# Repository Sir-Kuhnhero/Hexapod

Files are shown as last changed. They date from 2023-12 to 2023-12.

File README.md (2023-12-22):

Due to bandwidth limitations I was forced to remove some files. If you can't download some of the larger files, go to Printables. You should find the most important files there.
Printables: https://www.printables.com/model/606030-3d-printed-hexapod

# Overview #

Seems like you want to build a Hexapod. Don't know why but since you're here, might as well tell you about the most important features about my design:

1. Cheap: 120 € (see Parts (toBuy) file)
2. RGB: 271 individual RGB LEDs
3. Cable management: Cables are routed inside the leg. no cable loop that tangle
4. ORP compatible: compatible with the Open Robotic Platform modules
5. Bluetooth control: Remote control via phone app

If this hasn't convinced you might I suggest watching my videos on the design and build.

Leg: https://youtu.be/Ta3ILBvA57U

Body & first Steps: https://youtu.be/FBk1Pa01zQ4

# Build #

Since you are reading this I assume you are at least considering my design. I have some instructions on Instucatbles and Hackster.io if you want to take a look at that.
Instructables: https://www.instructables.com/3D-Printed-Hexapod/
Hackster.io: https://www.hackster.io/sir-kuhnhero/3d-printed-hexapod-05a60c

You can also find all the most important files on Printables: https://www.printables.com/model/606030-3d-printed-hexapod

All the 3mf files are oriented correctly with the needed support material. My parts are design in a way that uses minimal support material. See “Parts (toPrint)” Excel sheet.

If you don't know what and where to buy take a look at the "Parts (toBuy)" Excel sheet. Those are the parts I bought and where. You can also update the prices and it will automatically calculate the final price. Everything I listed is without shipping since that varies drastically.

If I didn't buy it or the link doesn't work anymore I linked to where I would buy.

# Wiring #



Connect everything like in the wiring diagram above. Be sure to use shielded wire for the connection between the STM32 and the servo drivers. I had some problems with interference without it.

One thing missing here is the XT60 connection between the battery and the rest of the circuit. You need a way to shut the hexapod down.

The LEDs are all connected in series in this order: Eye Centre, Eye middle ring, Eye outer ring, bottom ring, leg[ (front right) root -> tip (proceeding clockwise)

For the servos you can connect them to wherever is easiest. However you will need to set the channel for each servo in the "output.cpp" file correctly.

```
Leg[0].Servo[0].ch = 2;
Leg[0].Servo[1].ch = 1;
Leg[0].Servo[2].ch = 0;

Leg[1].Servo[0].ch = 6;
Leg[1].Servo[1].ch = 5;
Leg[1].Servo[2].ch = 4;

Leg[2].Servo[0].ch = 13;
Leg[2].Servo[1].ch = 14;
Leg[2].Servo[2].ch = 15;

Leg[3].Servo[0].ch = 18;
Leg[3].Servo[1].ch = 17;
Leg[3].Servo[2].ch = 16;

Leg[4].Servo[0].ch = 25;
Leg[4].Servo[1].ch = 26;
Leg[4].Servo[2].ch = 27;

Leg[5].Servo[0].ch = 29;
Leg[5].Servo[1].ch = 30;
Leg[5].Servo[2].ch = 31;
```

The Leg naming is as followes:

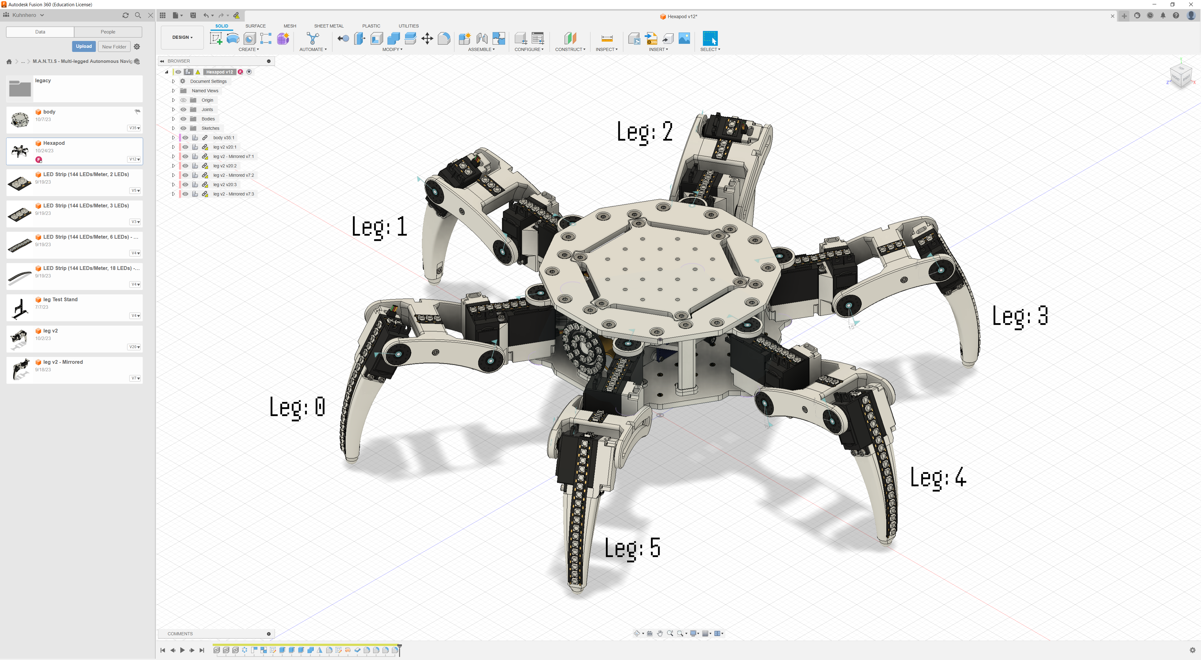
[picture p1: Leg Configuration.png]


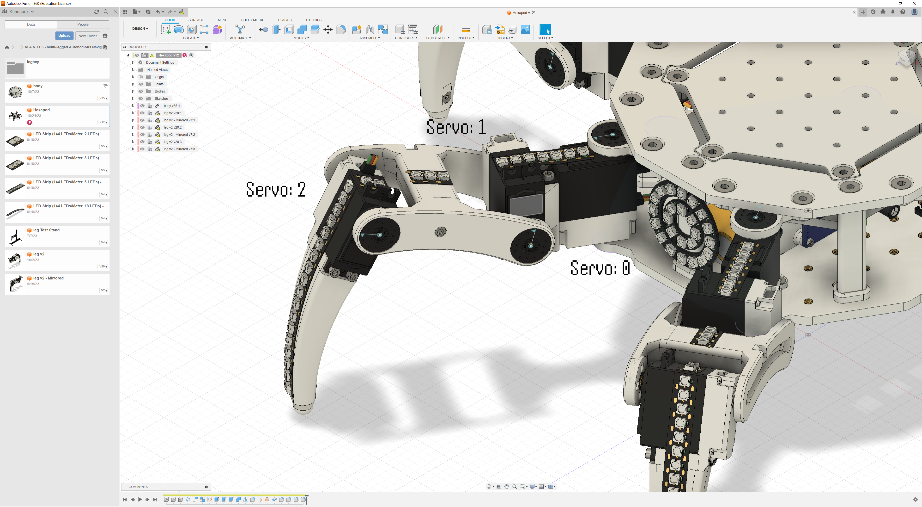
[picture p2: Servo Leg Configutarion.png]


On that node ensure that you bridge the first solder pad on one of the servo drivers. This will ensure that it uses a different I2C address. This second driver will continue the channel numbering of the first (16-31).

# Programming #

The code has been written in Visual Studio Code with the platform IO extension.

To Upload it make sure you have both installed and add the folder bellow as a project.

From here upload the code. Be sure to use an ST-Link for this. You can use a simple FTDI Programmer or something similar but you will have to unplug the Bluetooth module to connect it and change the "upload_protocol" in the platformio.ini file from "stlink" to what your programmer requires. Check [here](https://docs.platformio.org/en/latest/boards/ststm32/genericSTM32F103C8.html#board-ststm32-genericstm32f103c8) for more info.

```
[env:genericSTM32F103C8]
platform = ststm32
board = genericSTM32F103C8
framework = arduino
debug_tool = stlink
upload_protocol = stlink
lib_deps = 
  adafruit/Adafruit PWM Servo Driver Library@^2.4.1
  fastled/FastLED@^3.6.0
 ```

I had some issues with my ST-Link a while ago and had to switch to an FTDI programmer. This ended up looking like this:

```
[env:genericSTM32F103C8]
platform = ststm32
board = genericSTM32F103C8
framework = arduino
upload_protocol = serial
lib_deps = 
  adafruit/Adafruit PWM Servo Driver Library@^2.4.1
  fastled/FastLED@^3.6.0
 ```

If you want to deactivate some functions, for example the LEDs, for some reason you can do that in the "header.h" file by commenting out what you don’t want. This can be great for testing new features.

```
#define WS2812B_LED

#define SERVO
//#define SERVO_CALIBRATION

#define DEBUG
// #define DEBUG_SERIAL
// #define DEBUG_LED

#define BLUETOOTH
```

You will also need to fine tune the servo angles by setting the angleOffset for each servo in the output.cpp file. If you set your values correctly it should look something like this. To make this easier you can uncomment "#define SERVO_CALIBRATION" in the "header.h" file. This will move every leg to it's origin.

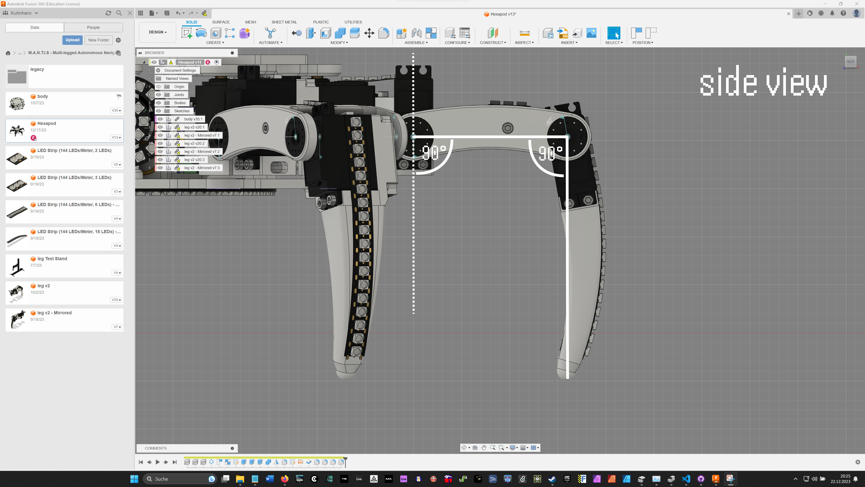
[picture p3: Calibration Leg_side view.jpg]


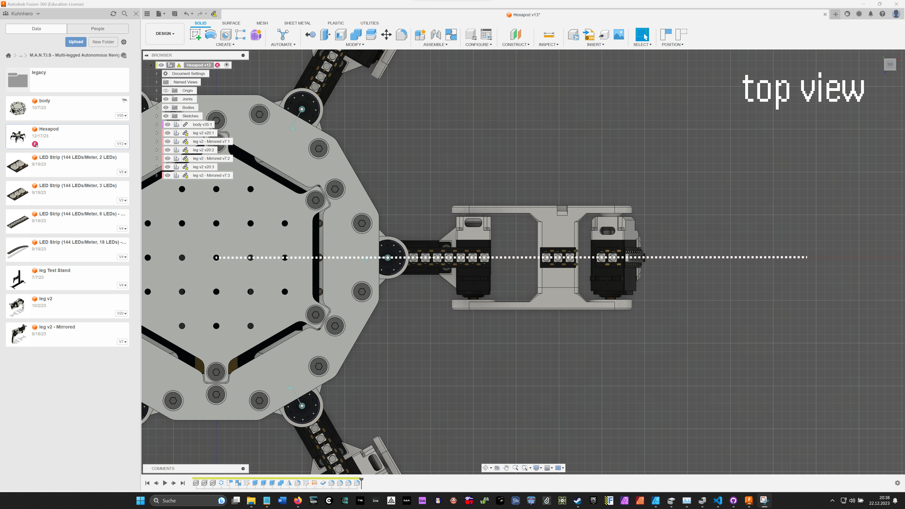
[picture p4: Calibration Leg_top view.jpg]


# Install Remote App & Connecting #

If you install the application you will get a message saying this might be dangerous to install. This is normal so don't worry. If you don't trust me take a look at the MIT App Inventor project files and compile it yourself.

Once installed make sure to allow "Nearby Devices". This is required for the app to find available Bluetooth devices.

Note that there are slider for controlling the Hexapods LEDs but that is currently disabled to reduce latency.

Turn your Hexapod on and pair to the Bluetooth module in you phones Bluetooth settings (only do this once). The default password is 1234 or 0000.

Now open the Hexapod Remote app and connect to the Bluetooth module. Once connected the Hexapod will have a simple startup animation and now you can control the hexapod using the two sticks.

Note that if you have changed something with #define at the beginning of header.h this behaviour might be different.

# Issues #

To be clear, my design is NOT perfect. Here are all the problems I have:

1. highly integrated leg design: routing the cables inside the leg looks awesome but makes assembly more difficult. If you were to not use LEDs this problem would largely be negated.
2. Current spikes: the hexapod is able to handle some load but especially at times of a power spike the Buck converter powering the servos can be insufficient. So you might want to use two or buy a more powerful one.
3. I2C buss instability: I had problems with the I2C buss between the STM32 and servo drivers breaking down causing the Hexapod to freeze. I was able to fix that by using shielded cables, but it required some trial and error.
4. incomplete Code: Not all features have been added in code. For example no LED animations beside the startup animation.

If you have any questions or suggestions consider writing me a comment.

Happy Making :)

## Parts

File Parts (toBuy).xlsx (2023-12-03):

 | Type | Lenght (mm) | number | price x1 (€) | price total (€) | Link (all provided links are where I bought or would buy and likely not the cheapest option). Prices may vary based on where, when and how you buy. If these Links are no longer valid just search for the Type.
Screws | M2 (Cub head) | 6 | 8 | 0.0248 | 0.1984 | https://www.aliexpress.com/item/1005001975621423.html
 | M3 (Cub head) | 10 | 12 | 0.0418 | 0.1672 | https://www.aliexpress.com/item/1005001975621423.html
 | M3 (Cub head) | 14 | 12 | 0.052 | 0.624 | https://www.aliexpress.com/item/1005001975621423.html
 | M3 (Cub head) | 20 | 6 | 0.0628 | 0.7536 | https://www.aliexpress.com/item/1005001975621423.html
 | M3 (Cub head) | 30 | 12 | 0.0792 | 0.4752 | https://www.aliexpress.com/item/1005001975621423.html
 | M3 (Countersunk) | 6 | 4 | 0.026 | 0.312 | https://www.aliexpress.com/item/4000020967604.html
 | M3 (Countersunk) | 10 | 4 | 0.0324 | 0.1296 | https://www.aliexpress.com/item/4000020967604.html
 | M5 (Countersunk) | 10 | 30 | 0.0382 | 1.146 | https://www.aliexpress.com/item/4000020967604.html
 | M3 nut (Square) |  | 48 | 0.0212 | 1.0176 | https://www.aliexpress.com/item/1005002179121598.html
 | M3 heat set insert (OD 5) | 5 | 53 | 0.0252 | 1.3356 | https://www.aliexpress.com/item/1005004490656289.html |  | You will only need 8 to build the Hexapod. The rest are for adding potential modules in the future
 | M5 heat set insert (OD 7) | 5 | 42 | 0.0502 | 2.1084 | https://www.aliexpress.com/item/1005004490656289.html
Electronics | STM32...C8T6 (BluePill) |  | 1 | 1.58 | 1.58 | https://www.aliexpress.com/item/1005003169244854.html
 | HC-05 |  | 1 | 2.11 | 2.11 | https://de.aliexpress.com/item/32967247206
 | PCA9865 (Servo driver) |  | 2 | 2.51 | 5.02 | https://www.aliexpress.com/item/32466332558.html
 | XL4016E1 (Buck converter) |  | 1 | 4.5 | 4.5 | https://www.aliexpress.com/item/33051908449.html
 | XL6009 (Blue Good) |  | 1 | 1.51 | 1.51 | https://de.aliexpress.com/item/1005005967596775.html
 | LED Ring | 60 | 1 | 5.83 | 5.83 | https://www.aliexpress.com/item/1005003185980117.html
 | LED Ring | 16 | 1 | 3 | 3 | https://www.aliexpress.com/item/4000877848238.html
 | LED Ring | 8 | 1 | 2 | 2 | https://www.aliexpress.com/item/4000877848238.html
 | LED Strip | 144LEDs/m | 2 | 7.28 | 14.56 | https://www.aliexpress.com/item/1005004129769604.html
 | 18650 Battery |  | 4 | 3.99 | 15.96 | https://www.18650batterystore.com/products/samsung-25r-18650
 | HX-2S-JH20 |  | 1 | 0.81 | 0.81 | https://www.aliexpress.com/item/1005002320527374.html
 | Wire | 1 m | 1 | 2.28 | 2.28 | https://www.aliexpress.com/item/1005001568846789.html
 | Wire | 1 m | 1 | 1.13 | 1.13 | https://www.aliexpress.com/item/1005001568846789.html
 | MGN996 Servo |  | 18 | 2.85 | 51.3 | https://www.aliexpress.com/item/33055771986.html
 | XT60 Female |  | 1 | 0.78 | 0.78 | https://www.aliexpress.com/item/1005003284718240.html
 | XT60 Male |  | 1 | 0.78 | 0.78 | https://www.aliexpress.com/item/1005003284718240.html
 |  |  |  |  | Total: |  | Shiping estimate:
 |  |  |  |  | 121.4176 |  | 0
 |  |  |  |  | Total (including Shiping estimate):
 |  |  |  |  | 121.4176
 | You will also need an ST-Link (or some other programmer) and a Phone.
Everything bellow are the parts above, only sorted for each subcomponent like Leg & Body and might be incomplete
Single Leg
Screws | Type | Length (mm) | number
 | M3 (Cub head) | 10 | 2
 | M3 (Cub head) | 14 | 2
 | M3 (Cub head) | 20 | 1
 | M3 (Cub head) | 30 | 2
 | M3 (Countersunk) | 10 | 1
 | M3 nut (Square) |  | 8
 | M5 heat set insert | 5 | 2
Electronics | LED Strip (LEDs) |  | 31
 | MGN996 Servo |  | 3
Body
Screws | Type | Lenght (mm) | number
 | M2 (Cub head) | 6 | 8
 | M3 (Countersunk) | 6 | 4
 | M3 (Countersunk) | 10 | 4
 | M5 (Countersunk) | 10 | 30
 | M3 heat set insert | 5.5 | 74
 | M5 heat set insert | 5 | 30
Electronics | STM32 (BluePill)
 | PCA9865 (Servo driver) |  | 2
 | XL4016E1 (Buck converter) |  | 1
 | LED ring 60 |  | 1
 | LED ring 16 |  | 1
 | LED ring 8 |  | 1
 | LED Strip (LEDs) |  | 1
 | 18650 Battery |  | 4
 | HX-2S-JH20 |  | 1
 | Wire
 | Wire

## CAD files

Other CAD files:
Hexapod_3D Models/body main_bottom.3mf
Hexapod_3D Models/body main_top.3mf
Hexapod_3D Models/leg/PLA_Tibia_main.3mf
Hexapod_3D Models/body/PLA_body spacer.3mf
Hexapod_3D Models/bushing_set.3mf
Hexapod_3D Models/leg Test Stand/test stand_mount.3mf
Hexapod_3D Models/leg/PLA_bushing.3mf
Hexapod_3D Models/body/body v35.3mf
Hexapod_3D Models/leg Test Stand/PLA-Coxa_bottom.3mf
Hexapod_3D Models/leg/PLA_Femur_left_mirrored.3mf
Hexapod_3D Models/leg_set_mirrored.3mf
Hexapod_3D Models/Hexapod v8.3mf
Hexapod_3D Models/leg Test Stand/PLA-90° Cuppler (40mm).3mf
Hexapod_3D Models/leg/PLA-Trochanter_Servo mount_mirrored.3mf
Hexapod_3D Models/leg Test Stand/leg Test Stand v4.3mf
Hexapod_3D Models/leg/PLA_Femur_right_mirrored.3mf
Hexapod_3D Models/leg Test Stand/test stand foot.3mf
Hexapod_3D Models/leg/PLA-Coxa_top.3mf
Hexapod_3D Models/Hexapod v8-rotated.3mf
Hexapod_3D Models/Hexapod v8.f3z
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

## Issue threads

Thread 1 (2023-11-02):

FastLED

Mordenkainen, 2023-11-02:
Was there something special to do to get the FastLED library working?

I am trying just a simple blink app and while it compiles and loads, no pin seems to be outputting the data signal. Was there a special version or something you used?

Mordenkainen, 2023-11-02:
User Error! SRY.

Closed 2023-11-02.

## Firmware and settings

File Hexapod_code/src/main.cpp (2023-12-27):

#include <Arduino.h>
#include <header.h>

int loopTime;

Vector2 directionInput(0, 0);
float rotationInput = 20;
float groundClearance = 35;
float stepRadius = 100;
float maxSpeed = 90;

State HexapodState = State::SITTING;

#ifdef WS2812B_LED
int ledUpdateTimer = 0;
int brightness = 5;
int colorR = 0;
int colorG = 0;
int colorB = 255;
bool ledUpdate = true;
#endif

void setup()
{
#ifdef BLUETOOTH
  Bluetooth_init();

  // don't continue until a connection has been established and a array of data has been recived
  while (Data[DATA_LENGTH - 1] == 0) // no data send can be 0
  {
    Bluetooth_read();
    delay(1);
  }

  Bluetooth_map();
#endif

#ifdef WS2812B_LED // initialitze LEDs
  Led_init();
#endif

#ifdef SERVO // initialite Servos
  Servo_init();
#endif

#ifdef WS2812B_LED // startup LED animation
  for (size_t i = 0; i < 25; i++)
  {
    Led_update(i);
    FastLED.show();
    delay(25);
  }

#ifdef SERVO
  for (int i = 0; i < 100; i++)
  {
    for (int o = 0; o < 6; o++)
    {
      LED_leg_animation(o, 0, float(i + 1) / 100.0f);
    }
    FastLED.show();

    delay(10);
  }
#endif

#endif

#ifdef SERVO
#ifdef BLUETOOTH
  Bluetooth_clear();
  Data[0] = 50;

  while (Data[0] == 50) // is 50 when it should sit down and 100 when it should stand up
  {
    Bluetooth_read();
    delay(10);
  }

  standUp();
#endif
#endif

#ifdef SERVO_CALIBRATION
  HexapodState = State::STANDING;
#endif
}

void loop()
{
  int long curTime = millis();

#ifdef BLUETOOTH
  Bluetooth_read();
  Bluetooth_map();
#endif

#ifdef SERVO

  // stand up and sit down as input suggests
  if (Data[0] == 50 && (HexapodState == State::STANDING || HexapodState == State::WALKING))
  {
    sitDown();
    curTime = millis(); // the sitDown function takes time so loopTime gets messed up
  }
  else if (Data[0] == 100 && HexapodState == State::SITTING)
  {
    standUp();
    curTime = millis(); // the sitDown function takes time so loopTime gets messed up
  }

  if (HexapodState == State::STANDING || HexapodState == State::WALKING)
  {
    walkCycle();
    Output_update();
  }
#endif

#ifdef WS2812B_LED
  // ping pong led blue color
  /*
    if (colorBDirection == 0)
    {
      colorB--;
    }
    else if (colorBDirection == 1)
    {
      colorB++;
    }

    if (colorB == 0)
    {
      colorBDirection = 1;
    }
    else if (colorB == 255)
    {
      colorBDirection = 0;
    }
  */

  if (ledUpdate || (ledUpdateTimer > updateInterval && continuesUpdate))
  {

    for (size_t i = 0; i < NUM_LEDS; i++)
    {
      Led_update(i);
    }

    FastLED.setBrightness(brightness);
    FastLED.show();

    ledUpdate = false;
    ledUpdateTimer = 0;

#ifdef BLUETOOTH
    // Bluetooth_clear(); // updating every led takes time
#endif
    curTime = millis();
  }

  ledUpdateTimer += loopTime;
#endif

  loopTime = millis() - curTime;
}

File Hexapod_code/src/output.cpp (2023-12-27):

#include <Arduino.h>
#include "header.h"

// ================================================================
// ===                          Servo                           ===
// ================================================================
#ifdef SERVO

Adafruit_PWMServoDriver servoDriver_0 = Adafruit_PWMServoDriver();
Adafruit_PWMServoDriver servoDriver_1 = Adafruit_PWMServoDriver(0x41);

Leg_Struct Leg[6];

void Servo_init()
{
    servoDriver_0.begin();
    servoDriver_0.setOscillatorFrequency(27000000);
    servoDriver_0.setPWMFreq(SERVO_FREQ); // Analog servos run at ~50 Hz updates

    servoDriver_1.begin();
    servoDriver_1.setOscillatorFrequency(27000000);
    servoDriver_1.setPWMFreq(SERVO_FREQ); // Analog servos run at ~50 Hz updates

#pragma region configureServos

// for correct Servo Placenment check the Leg Configuration and Servo Leg Configuration Images
#pragma region Leg_0
    Leg[0].Servo[0].ch = 2;
    Leg[0].Servo[1].ch = 1;
    Leg[0].Servo[2].ch = 0;

    Leg[0].Servo[2].minAngle = 20;
    Leg[0].Servo[2].maxAngle = 160;

    Leg[0].Servo[0].angleOffset = 0;
    Leg[0].Servo[1].angleOffset = -10;
    Leg[0].Servo[2].angleOffset = -5;

    Leg[0].mirrored = true;
    Leg[0].mountAngle = -30;

    Leg[0].minLED = 85;
    Leg[0].maxLED = 115;
#pragma endregion

#pragma region Leg_1
    Leg[1].Servo[0].ch = 6;
    Leg[1].Servo[1].ch = 5;
    Leg[1].Servo[2].ch = 4;

    Leg[1].Servo[2].minAngle = 20;
    Leg[1].Servo[2].maxAngle = 160;

    Leg[1].Servo[0].angleOffset = -10;
    Leg[1].Servo[1].angleOffset = 0;
    Leg[1].Servo[2].angleOffset = 12;

    Leg[1].mirrored = true;
    Leg[1].mountAngle = -90;

    Leg[1].minLED = 116;
    Leg[1].maxLED = 146;
#pragma endregion

#pragma region Leg_2
    Leg[2].Servo[0].ch = 13;
    Leg[2].Servo[1].ch = 14;
    Leg[2].Servo[2].ch = 15;

    Leg[2].Servo[2].minAngle = 20;
    Leg[2].Servo[2].maxAngle = 160;

    Leg[2].Servo[0].angleOffset = -12;
    Leg[2].Servo[1].angleOffset = -10;
    Leg[2].Servo[2].angleOffset = -16;

    Leg[2].mirrored = true;
    Leg[2].mountAngle = -150;

    Leg[2].minLED = 147;
    Leg[2].maxLED = 177;
#pragma endregion

#pragma region Leg_3
    Leg[3].Servo[0].ch = 18;
    Leg[3].Servo[1].ch = 17;
    Leg[3].Servo[2].ch = 16;

    Leg[3].Servo[2].minAngle = 20;
    Leg[3].Servo[2].maxAngle = 160;

    Leg[3].Servo[0].angleOffset = -1;
    Leg[3].Servo[1].angleOffset = 6;
    Leg[3].Servo[2].angleOffset = 44;

    Leg[3].mirrored = false;
    Leg[3].mountAngle = 150;

    Leg[3].minLED = 178;
    Leg[3].maxLED = 208;
#pragma endregion

#pragma region Leg_4
    Leg[4].Servo[0].ch = 25;
    Leg[4].Servo[1].ch = 26;
    Leg[4].Servo[2].ch = 27;

    Leg[4].Servo[2].minAngle = 20;
    Leg[4].Servo[2].maxAngle = 160;

    Leg[4].mirrored = false;
    Leg[4].mountAngle = 90;

    Leg[4].Servo[0].angleOffset = -5;
    Leg[4].Servo[1].angleOffset = -10;
    Leg[4].Servo[2].angleOffset = -8;

    Leg[4].minLED = 209;
    Leg[4].maxLED = 239;
#pragma endregion

#pragma region Leg_5
    Leg[5].Servo[0].ch = 29;
    Leg[5].Servo[1].ch = 30;
    Leg[5].Servo[2].ch = 31;

    Leg[5].Servo[2].minAngle = 20;
    Leg[5].Servo[2].maxAngle = 160;

    Leg[5].Servo[0].angleOffset = -2;
    Leg[5].Servo[1].angleOffset = 3;
    Leg[5].Servo[2].angleOffset = -20;

    Leg[5].mirrored = false;
    Leg[5].mountAngle = 30;

    Leg[5].minLED = 240;
    Leg[5].maxLED = 270;

#pragma endregion
    for (int i = 0; i < int(sizeof(Leg) / sizeof(Leg[0])); i++)
    {
        Leg[i].Servo[1].minAngle = 0;
        Leg[i].Servo[1].maxAngle = 180;
    }

#pragma endregion
}

void Servo_update(const Servo_Struct &servo, const int &onValue)
{
    int angle = constrain(servo.targetAngle, servo.minAngle, servo.maxAngle);
    // check which servo driver to use
    if (servo.ch < 16)
        servoDriver_0.setPWM(servo.ch, onValue, SERVO_BASELINE + (angle + servo.angleOffset) * 2);
    else if (servo.ch < 32)
        servoDriver_1.setPWM(servo.ch - 16, onValue, SERVO_BASELINE + (angle + servo.angleOffset) * 2);
}

void Servo_update(const int &servoCH, const int &angle, const int &onValue)
{
    // check which servo driver to use
    if (servoCH < 16)
        servoDriver_0.setPWM(servoCH, onValue, SERVO_BASELINE + angle * 2);
    else if (servoCH < 32)
        servoDriver_1.setPWM(servoCH - 16, onValue, SERVO_BASELINE + angle * 2);
}

// turns off the output for the servo
void Servo_deactivateAll()
{
    // loop through each leg
    for (size_t i = 0; i < 6; i++)
    {
        // loop through each servo in leg
        for (size_t o = 0; o < 3; o++)
        {
            Servo_update(Leg[i].Servo[o], 4096);
        }
    }
}

// used to test wether min values are correct
void Servo_moveAllToMinValue()
{
    // loop through each leg
    for (size_t i = 0; i < 6; i++)
    {
        // loop through each servo in leg
        for (size_t o = 0; o < 3; o++)
        {
            int oldTargetAngle = Leg[i].Servo[o].targetAngle;

            Leg[i].Servo[o].targetAngle = Leg[0].Servo[o].minAngle - abs(Leg[0].Servo[o].angleOffset);

            Servo_update(Leg[i].Servo[o]);

            Leg[i].Servo[o].targetAngle = oldTargetAngle;
        }
    }
}

// used to test wether max values are correct
void Servo_moveAllToMaxValue()
{
    // loop through each leg
    for (size_t i = 0; i < 6; i++)
    {
        // loop through each servo in leg
        for (size_t o = 0; o < 3; o++)
        {
            int oldTargetAngle = Leg[i].Servo[o].targetAngle;

            Leg[i].Servo[o].targetAngle = Leg[0].Servo[o].maxAngle + abs(Leg[0].Servo[o].angleOffset);

            Servo_update(Leg[i].Servo[o]);

            Leg[i].Servo[o].targetAngle = oldTargetAngle;
        }
    }
}

void Leg_update(const int &legID)
{
    calcLegServoAngles(Leg[legID]);

    Servo_update(Leg[legID].Servo[0]);
    Servo_update(Leg[legID].Servo[1]);
    Servo_update(Leg[legID].Servo[2]);
}

// update every output as needed to reflect any changes
void Output_update()
{
    Leg_update(0);
    Leg_update(1);
    Leg_update(2);
    Leg_update(3);
    Leg_update(4);
    Leg_update(5);
}

#endif

// ================================================================
// ===                           LED                            ===
// ================================================================
#ifdef WS2812B_LED

CRGB leds[NUM_LEDS];

void Led_init()
{
    FastLED.addLeds<WS2812B, DATA_PIN, RGB>(leds, NUM_LEDS); // GRB ordering is typical

    FastLED.setBrightness(brightness);

    // turn all led off
    for (size_t i = 0; i < NUM_LEDS; i++)
    {
        leds[i] = CRGB::Black;
    }
    FastLED.show();
}

void Led_update(const int &ledID)
{
    leds[ledID] = CRGB(uint8_t(float(colorG) * 2.5f), uint8_t(float(colorR) * 2.5f), uint8_t(float(colorB) * 2.5f));
}

void Led_update(const int &ledID, CRGB color)
{
    leds[ledID] = color;
}
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

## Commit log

2023-01-24 servo actuator
2023-08-24 3d models
    [Coxa-bottom.3mf, Coxa-top.3mf, Femur-Servo mount.3mf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]
2023-08-26 full Hexapod framework
    IK for the each leg of the full hexapod has been finished. No full Hexapod IK has been implemented. LEDs and startup sequence have been implemented.
2023-08-29 fixed IK, added circleProjection
    Fixed an issue that made it impossible to move the legs in the y axis. There is now also a function to project a point onto a sphere through a vector (not fully tested).
    [debug.cpp, header.h, ik.cpp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]
2023-09-01 added basic walking
    the hexaod can now take steps. Lifting the legs is still very unsmothe and sudden but changes are in the works
2023-09-03 walking now working
    The Hexapod now properly lift it's legs for each steps. This works in every direction.
2023-09-09 code cleanup
    removed some unused code and added a way to use an external arduino as a crude debugger
2023-09-11 walk gait restructure
    very simmilar code as before only more readable. Additionally the leg calculation is done for each leg in preperation for rotation
2023-09-12 improved walking start
    Hexapod now starts liften each leg to maximise the length of the first step
2023-09-12 partial rotation
    Legs are moving in a concentric circle. However for some reason the Path of Leg 0 & 5 as well as 2 & 3 are swaped.
    [header.h, main.cpp]
2023-09-12 rotation working
    Turns out there was a missplaced - in the inverse kinematics :)
2023-09-14 correct movement
    Values received are now correctly converted to value input for the walking algorithm
    [header.h, main.cpp]
2023-09-17 more remote features
    Some more features for controlling the Hexapod. The LEDs are not working for some reason. They are just alway white with 100% brightness.
    [header.h, main.cpp, output.cpp]
2023-09-28 LED controll
    User can now in theory controll the color and brightness of the LEDs. However this has been deactivated to lower latency and make the hexapod movements more responsive.
2023-10-07 addded 3d models
    updated 3d models are now included
    [Hexapod v8-rotated.3mf, Hexapod v8.3mf, Hexapod v8.f3z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]
2023-10-08 Aditional files
    More models and MIT App Inventor source code.
    [PLA-Trochanter_Servo mount_mirrored.3mf, PLA-Trochanter_Servo mount_mirrored.stl, PLA_Femur_left_mirrored.3mf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]
2023-10-08 wiring diagram
2023-11-02 removed some large files
    I removed some large files since GitHub only allows for a specific ammount of bandwith.
    [Coxa-bottom.3mf, Coxa-top.3mf, Femur-Servo mount.3mf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]
2023-11-08 missing Bluetooth module
    [Parts (toBuy).xlsx]
2023-12-03 Parts (toBuy) list
    [Parts (toBuy).xlsx]
2023-12-17 Leg and Servo Configuration
2023-12-22 Add Calibration routine
    I previously remove my code for calibration the servo offset. You can now simply uncomment #define SERVO_CALIBRATION to tell go into servo calibration mode
    [Mustache.3mf, PLA-90° Cuppler (40mm).stl, PLA-Coxa_bottom.stl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]
2023-12-27 Add Remote led controll
    The user can now control the color of the LEDs. There were originally issues with latency, but these have been resolved.
    [bluetooh.cpp, header.h, main.cpp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]
